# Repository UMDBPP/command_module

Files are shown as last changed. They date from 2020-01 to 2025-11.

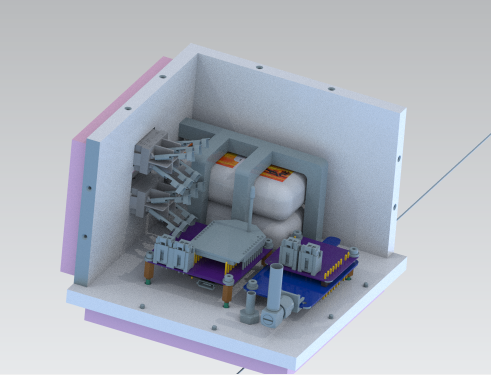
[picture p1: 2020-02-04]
Design_Review/images/cell_box.PNG

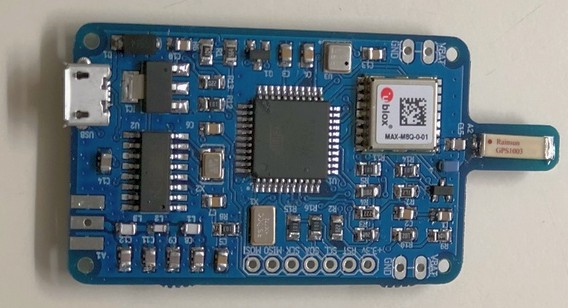
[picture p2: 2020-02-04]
Design_Review/images/lightaprs.jpg

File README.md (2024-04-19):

# ```</CMD>```

Command is the primary tracking payload flown by BPP. This repository contains design files and software required to run the current version of command.

Current POC:
Shipman

 ## Design Priciples
As the command module needs to fly on every flight mass reduction is a primary focus. For this reason a switch from perfboard to custom PCB's was done, and a substantial reduction in box volume is underway. Reliability is incredibly important and for this reason the payload operates its tracking systems in a full 4N redundant method.
### Tracking systems include (system/function):
#### 2x LiteAPRS 2m transmitters on 144.390 MHz
In flight position updates every minute. By nature of APRS tracking in hilly terrain unlikely to receive exact coordinates under 500m unless operating our own radios.
#### 1x SPOT Trace Tracker
COTS tracker from SPOT. Gives exact coordinates on landing.
#### 1x BITS (Balloon Iridium Telemetry System)
Exact coordinates throughout the flight, variable transmission rate 1min-15minutes (technically 10s-inf). Datalogger. XBee 900 HP allows for commands to be relayed through Iridium to other payloads and telemetry from payloads to be sent to ground. Possibility of ground to payload XBee communication without Iridium allowing for low latency high rate commanding.

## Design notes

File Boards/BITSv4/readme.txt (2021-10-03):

Folder for BITSv4 development
Starting 10/3/2021,
jmolter

Work based on lessons from BITSv3

---Focus Areas---

-Reg LMR16020-
Keep the IC
Change inductor for easier assembly
Consider chaning output to 5v,
OR source 5v from another source

-Misc.-
Change power connector to match LightAPRS LVC

Change picoblade to right angle

Remove celltracker crosstalk conn

Consider GPS improvements

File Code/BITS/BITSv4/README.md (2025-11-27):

# BITS (Balloon Iridium Telemetry System)
The UMDBPP Iridium payload, armed with an Iridium 9603 on a RockBlock carrier board for instantaneous Global Blackmagics

WIP: XBee Mesh net support for other payloads
     New PCB for smaller, lighter, better looking tracking
     Battery Voltage sensing for long haul flights

# Building Code
Hi, from the `BITS` folder, run `arduino-cli compile -e BITSv4` to do reproducible builds. I also created a Github Action that will automatically build the BITSv4 code when you push any changes to the master branch. You can find the build artifacts at [https://github.com/UMDBPP/command_module/releases](https://github.com/UMDBPP/command_module/releases).

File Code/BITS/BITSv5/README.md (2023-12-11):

# ```</BITSv5 Software>```

This folder contains the code needed to operate BITS (Balloon Iridium Telemetry System) Version 5. The below outlines the structure of the code. BITS Version 5 uses the RP2040 by the Raspberry Pi foundation and leverages the RP2040 Pico C SDK and build system meaning that this is not an Arduino based project!

The test project below currently features 3 executable binaries that are automatically built using a GitHub action. This is a proof of concept and enables the BITSv5 software to be built independent of any single user which makes the process of changing and rebuilding the project more approachable to everyone.

The action that builds the test project can be seen here: [https://github.com/UMDBPP/command_module/actions/workflows/build-BITSv5.yml](https://github.com/UMDBPP/command_module/actions/workflows/build-BITSv5.yml)

And the release product that it creates can be seen here: [https://github.com/UMDBPP/command_module/releases/tag/BITSv5-v0.0.0](https://github.com/UMDBPP/command_module/releases/tag/BITSv5-v0.0.0)

## Test
This is the current working space for developing BITSv5 software. Currently basic radio communications have been implemented and verified with hardware. Below are features that need to be implemented for a minimum viable product in the the next month or two.

[x] Basic long range radio communications

[] Serial console

[] Non-volatile configuration

[] GPS geolocation

[] Iridium interface and comms

## Radio Test
This is a future project designed to be a suite of tests that test the radio found on BITSv5. Not currently implemented.

## Pico-SDK
This is a submodule that pulls in the RP2040 SDK which is required to build all of the code found in this folder. It shouldn't need to be touched except for the occasional update.

More on the RP2040 C SDK can be found here: [https://www.raspberrypi.com/documentation/pico-sdk/](https://www.raspberrypi.com/documentation/pico-sdk/)

## Reference
This folder contains two useful documents from the Raspberry Pi Foundation about using the SDK above.

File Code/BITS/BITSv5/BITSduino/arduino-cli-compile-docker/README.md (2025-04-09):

# A Note

This is originally from https://github.com/MacroYau/arduino-cli-compile-docker. I made some modifications since I think the cli has changed since the repo was originally made. The reason that I recommend this build system is to avoid the messiness that comes with having different global libaries installed on different systems. Instead the build environment is created ad hoc as a docker container which means that it should be much easier for anyone to build the code.

-Shipman

# Arduino CLI Compile



Dockerized [`arduino-cli`](https://github.com/arduino/arduino-cli) sketch 
compilation tool with per-project core and library dependencies support.

## Getting Started

1.  Install [Docker Engine](https://docs.docker.com/install/) on your machine.

2.  Go to your Arduino sketch folder which contains the main `.ino` file.

3.  Create `project.yaml` with the following content:

    ```yaml
    # Filename of the project's main sketch
    sketch: Blink.ino
    # Sketch version (optional; appended to filename of compiled binary file)
    version: 1.0.0

    # Compilation target
    target:
      # Arduino core name
      core: arduino:samd            # Installs the latest version; or
      # core: arduino:samd==1.6.21  # Installs v1.6.21
      # Arduino board FQBN string (obtained from `arduino-cli board list`)
      board: arduino:samd:mkrzero
      # Additional board manager URL for core installation (optional)
      url: https://arduino.esp8266.com/stable/package_esp8266com_index.json

    # Libraries to be included for compilation
    libraries:
      - Arduino Low Power           # Installs the latest version; or
      # - Arduino Low Power==1.2.1  # Installs v1.2.1
    ```

4.  Download `arduino-cli-compile` to a `PATH` directory and make it executable.

5.  Run `arduino-cli-compile path/to/sketch/folder`.

6.  The compiled binary file will appear in `dist/` inside the sketch folder.

7.  Upload the compiled binary file to your Arduino board. This part is not 
    (yet) Dockerized. For example, you can use `arduino-cli` installed on your 
    machine connecting to the board:

    ```bash
    arduino-cli upload -p /dev/ttyACM0 -b arduino:samd:mkrzero -i path/to/bin/file
    ```

8.  Watch your board blinking!

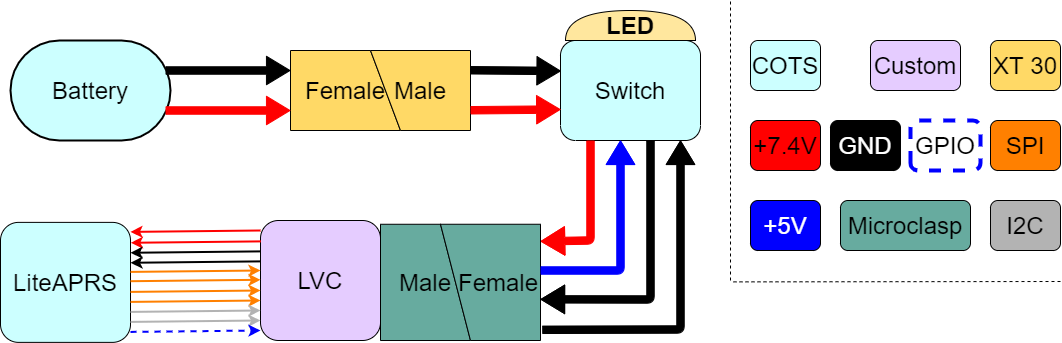
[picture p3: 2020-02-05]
Design_Review/images/liteaprs_block_diagram.png

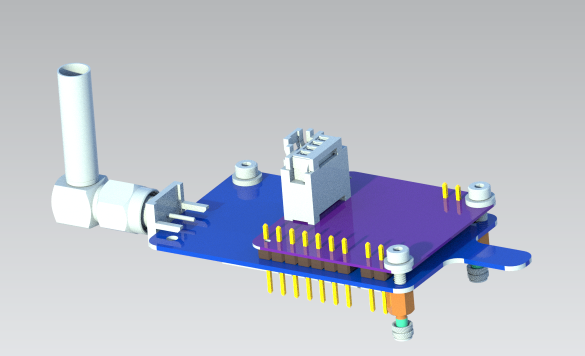
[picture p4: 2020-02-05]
Design_Review/images/LVC.PNG

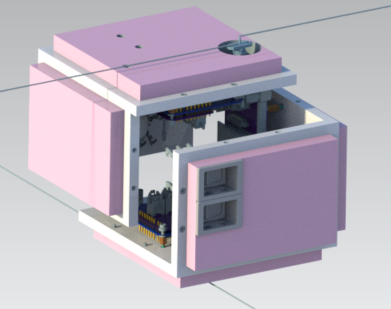
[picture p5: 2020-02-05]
Design_Review/images/opened_cmd.PNG

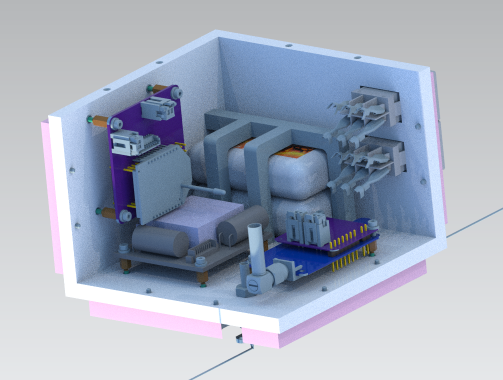
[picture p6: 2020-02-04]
Design_Review/images/iridium_box.PNG

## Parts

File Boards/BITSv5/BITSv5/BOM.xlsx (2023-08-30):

Part ID | Name | Function | Value | Package | Part Link | Cost
U1 | RP2040 | Microprocessor | - | - | https://www.digikey.com/en/products/detail/raspberry-pi/SC0914-13/14306010?s=N4IgTCBcDaIE4AcwAYAsyQF0C%2BQ | $0.70
U2 | W25Q128JVS | Flash Memory | 16MB | - | https://www.digikey.com/en/products/detail/winbond-electronics/W25Q128JVSIQ/5803943 | $1.68
U3 | MAX-M10S | GPS | - | MAX | https://www.digikey.com/en/products/detail/u-blox/MAX-M10S-00B/15712906 | $21.00
U4 | MAX25255AFDA/VY+ | Dual Buck | 3.3V, 5V | 23-WFQFN | https://www.digikey.com/en/products/detail/analog-devices-inc-maxim-integrated/max25255afda-vy/18693435 | $2.41
U6 | XBP9X-DMUS-001 | Xbee | 900 MHz | SMT | https://www.digikey.com/en/products/detail/digi/XBP9X-DMUS-001/5972744 | $112.59
U7 | TPS2121 | Power Mux Switch | 2:1 In:Out | 12-VFQFN | https://www.digikey.com/en/products/detail/texas-instruments/TPS2121RUXR/9859001 | $2.31
U8 | LTC6703 | LVC Comparator | 3V Cutoff | 3-DFN | https://www.digikey.com/en/products/detail/analog-devices-inc/LT6703HDC-3-TRMPBF/1590279 | $3.05
U9 | TVS1800 | Surge Protection | - | 6-WDFN | https://www.digikey.com/en/products/detail/texas-instruments/TVS1800DRVR/8601784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 | $0.65
U10 | USBLC6-2SC6 | Surge Protection | - | SOT-23-6 | https://www.digikey.com/en/products/detail/stmicroelectronics/USBLC6-2SC6/1040559 | $0.61
Y1 | ECS-120-10-36B2-JTN-TR | Crystal | 12 MHz | 2520 | https://www.digikey.com/en/products/detail/ecs-inc/ECS-120-10-36B2-JTN-TR/14663300 | $0.42
BT1 | XT30PW-M | Battery Connector | - | XT30
AE1 | 1575AT43A0040001E | GPS Antenna | 0.5-1 dB | Chip | https://www.digikey.com/en/products/detail/johanson-technology-inc/1575AT43A0040001E/1560674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 | $0.89
D1 |  | LED |  | 0603
J1 | Rockblock Connector | Iridium | 10-Pin | Molex PB | https://www.digikey.com/en/products/detail/molex/0532611071/699102 | $1.07 | must order connecting pieces
J2 | USB-C 2.0 Port | USB C Connection | - | GCT4085 | https://www.digikey.com/en/products/detail/gct/USB4085-GF-A/9859662 | $0.94
J3 | Headers | Debugging | - | Male Pins | - | -
SW2 | CAS-120TB | Memory Boot | - | - | https://www.digikey.com/en/products/detail/nidec-components-corporation/CAS-120TB/341662 | $1.37
SW3 | CL-SB-12B-01T | Power Slider | - | - | https://www.digikey.com/en/products/detail/nidec-components-corporation/CL-SB-12B-01T/3507823 | $1.26
Q1 |  | Transistor | PNP | SOT23-3
Q2 |  | Transistor | NPN | SOT23
R1 |  | R | 27 | 0402
R2 |  | R | 27 | 0603
R3 |  | R | 10K | 0603
R4 |  | R | 1K | 0603
R5 |  | R | 1K | 0402
R7 |  | R | 5.1K | 0603
R8 |  | R | 5.1K | 0603
R9 |  | R | 10K | 0603
R10 |  | R | 10K | 0603
R11 |  | R | 10K | 0603
R12 |  | R | 470 | 0603
R15 |  | R | 23.7K | 0603
R16 |  | R | 5K | 0603
R17 |  | R | 46.4K | 0603
R18 |  | R | 1.5M | 0603
R19 |  | R | 100K | 0603
R20 |  | R | 510K | 0603
R21 |  | R | 10K | 0603
R22 |  | R | 23.7K | 0603
R23 |  | R | 5K | 0603
R24 |  | R | 10K | 0603
C1 |  | C | 1 uF | 0402
C2 |  | C | 1 uF | 0402
C3 |  | C | 100 nF | 0402
C4 |  | C | 100 nF | 0402
C5 |  | C | 100 nF | 0402
C6 |  | C | 100 nF | 0402
C7 |  | C | 100 nF | 0402
C8 |  | C | 100 nF | 0402
C9 |  | C | 100 nF | 0402
C10 |  | C | 100 nF | 0402
C11 |  | C | 100 nF | 0402
C12 |  | C | 100 nF | 0603
C13 |  | C | 10 pF | 0603
C14 |  | C | 10 pF | 0603
C15 |  | C | 0.1 uF | 0603
C16 |  | C | 4.7 uF | 0603
C17 |  | C | 22 uF | 0603
C18 |  | C | 22 uF | 0603
C19 |  | C | 22 uF | 0603
C20 |  | C | 22 uF | 0603
C21 |  | C | 22 uF | 0603
C22 |  | C | 22 uF | 0603
C23 |  | C | 0.1 uF | 0603
C24 |  | C | 0.1 uF | 0603
C25 |  | C | 2.2 uF | 0603
C26 |  | C | 100 pF | 0603
C27 |  | C | 1 uF | 0603
C28 |  | C | 10 uF | 0603
C29 |  | C | 4.7 uF | 0603
C30 |  | C | 4.7 uF | 0603
C31 |  | C | 0.1 uF | 0603
C32 |  | C | 100 nF | 0603
C33 |  | C | 10 nF | 0603
C34 |  | C | 10 uF | 0603
C35 |  | C | 10 uF | 0603
C36 |  | C | 1 uF | 0603
C37 |  | C | 1 uF | 0603
L1 | 252012CDMCDDS-R47MC | L | 0.47 uH | 1008 | https://www.digikey.com/en/products/detail/sumida-america-inc/252012CDMCDDS-R47MC/9960783 | $0.55
L2 | 252012CDMCDDS-R47MC | L | 0.47 uH | 1008 | https://www.digikey.com/en/products/detail/sumida-america-inc/252012CDMCDDS-R47MC/9960783 | $0.55
 |  |  |  |  | Total | $152.05

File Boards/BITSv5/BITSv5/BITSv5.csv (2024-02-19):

Source: | /Users/michaelshipman/Developer/command_module/Boards/BITSv5/BITSv5/BITSv5.kicad_sch
Date: | 2024 February 18, Sunday 18:52:49
Tool: | Eeschema 7.0.5-0
Generator: | /Applications/KiCad/KiCad.app/Contents/SharedSupport/plugins/bom_csv_grouped_by_value_with_fp.py
Component Count: | 103
Ref | Qnty | Value | Cmp name | Footprint | Description | Vendor | DNP
B1 | 1 | KMR2 | SW_Push | Button_Switch_SMD:SW_Push_1P1T_NO_CK_KMR2 | Push button switch, generic, two pins
BT2 | 1 | 3V | Battery_Cell | BITSv5:SEIKO_ML414H_IV01E | Single-cell battery
C1, C2 | 2 | 1uF | C_Small | Capacitor_SMD:C_0402_1005Metric | Unpolarized capacitor, small symbol
C3, C4, C5, C6, C7, C8, C9, C10, C11, C12, C32 | 11 | 100nF | C_Small | Capacitor_SMD:C_0402_1005Metric | Unpolarized capacitor, small symbol
C13, C14 | 2 | 10pF | C_Small | Capacitor_SMD:C_0402_1005Metric | Unpolarized capacitor, small symbol
C15, C26, C34 | 3 | 10uF | C_Small | Capacitor_SMD:C_0603_1608Metric | Unpolarized capacitor, small symbol
C16, C17, C24, C27, C33, C39, C40 | 7 | 1uF | C_Small | Capacitor_SMD:C_0603_1608Metric | Unpolarized capacitor, small symbol
C18, C20 | 2 | 47uF | C_Small | Capacitor_SMD:C_1206_3216Metric | Unpolarized capacitor, small symbol
C19, C23, C29, C30 | 4 | 100nF | C_Small | Capacitor_SMD:C_0603_1608Metric | Unpolarized capacitor, small symbol
C21 | 1 | 4.7uF | C_Small | Capacitor_SMD:C_0805_2012Metric | Unpolarized capacitor, small symbol
C25, C31 | 2 | 22uF | C_Small | Capacitor_SMD:C_0805_2012Metric | Unpolarized capacitor, small symbol
C28, C38 | 2 | 15uF | C_Small | Capacitor_SMD:C_1206_3216Metric | Unpolarized capacitor, small symbol
D1 | 1 | LED | LED | LED_SMD:LED_0603_1608Metric | Light emitting diode
D2 | 1 | 0.5A/40V/240mV | D_Schottky_Small | Diode_SMD:D_SOD-123F | Schottky diode, small symbol
H1, H2, H3 | 3 | M2 | MountingHole_Pad | MountingHole:MountingHole_2.2mm_M2_Pad | Mounting Hole with connection
J1 | 1 | Conn_01x03_Pin | Conn_01x03_Pin | Connector_PinHeader_2.54mm:PinHeader_1x03_P2.54mm_Vertical | Generic connector, single row, 01x03, script generated
J2 | 1 | USB_C_Receptacle_USB2.0 | USB_C_Receptacle_USB2.0 | Connector_USB:USB_C_Receptacle_GCT_USB4105-xx-A_16P_TopMnt_Horizontal | USB 2.0-only Type-C Receptacle connector
J3 | 1 | XT30 | Conn_01x02 | Connector_AMASS:AMASS_XT30PW-M_1x02_P2.50mm_Horizontal | Generic connector, single row, 01x02, script generated (kicad-library-utils/schlib/autogen/connector/)
J4 | 1 | PicoBlade_53261-1071 | Conn_01x10_Pin | Connector_Molex:Molex_PicoBlade_53261-1071_1x10-1MP_P1.25mm_Horizontal | Generic connector, single row, 01x10, script generated
J5, J6 | 2 | U.FL | Conn_Coaxial | Connector_Coaxial:U.FL_Molex_MCRF_73412-0110_Vertical | coaxial connector (BNC, SMA, SMB, SMC, Cinch/RCA, LEMO, ...)
JP1 | 1 | SolderJumper_2_Open | SolderJumper_2_Open | Jumper:SolderJumper-2_P1.3mm_Open_RoundedPad1.0x1.5mm | Solder Jumper, 2-pole, open
L3, L4 | 2 | 3.3uH | L_Small | Inductor_SMD:L_1210_3225Metric | Inductor, small symbol
Q1 | 1 | Q_NMOS_GSD | Q_NMOS_GSD | Package_TO_SOT_SMD:SOT-23-3 | N-MOSFET transistor, gate/source/drain
R1, R2 | 2 | 27 | R_Small | Resistor_SMD:R_0402_1005Metric | Resistor, small symbol
R3, R6, R9, R22, R27 | 5 | DNF | R_Small | Resistor_SMD:R_0603_1608Metric | Resistor, small symbol
R4 | 1 | 1K | R_Small | Resistor_SMD:R_0603_1608Metric | Resistor, small symbol
R5 | 1 | 1K | R_Small | Resistor_SMD:R_0402_1005Metric | Resistor, small symbol
R7, R8 | 2 | 5.1K | R_Small | Resistor_SMD:R_0603_1608Metric_Pad0.98x0.95mm_HandSolder | Resistor, small symbol
R10, R13 | 2 | 100m | R_Small | Resistor_SMD:R_0603_1608Metric | Resistor, small symbol
R11 | 1 | 10k | R_Small | Resistor_SMD:R_0603_1608Metric | Resistor, small symbol
R12 | 1 | 470 | R_Small | Resistor_SMD:R_0603_1608Metric | Resistor, small symbol
R14 | 1 | 3.3K | R_Small | Resistor_SMD:R_0603_1608Metric | Resistor, small symbol
R15 | 1 | 332k | R_Small | Resistor_SMD:R_0603_1608Metric | Resistor, small symbol
R16, R20, R31 | 3 | 100k | R_Small | Resistor_SMD:R_0603_1608Metric | Resistor, small symbol
R17 | 1 | 44.2K | R_Small | Resistor_SMD:R_0603_1608Metric | Resistor, small symbol
R21, R24 | 2 | 10K | R_Small | Resistor_SMD:R_0603_1608Metric | Resistor, small symbol
R23, R28 | 2 | 0 | R_Small | Resistor_SMD:R_0603_1608Metric | Resistor, small symbol
R25 | 1 | 10.2k | R_Small | Resistor_SMD:R_0603_1608Metric | Resistor, small symbol
R26 | 1 | 5k | R_Small | Resistor_SMD:R_0603_1608Metric | Resistor, small symbol
R29 | 1 | 15k | R_Small | Resistor_SMD:R_0603_1608Metric | Resistor, small symbol
R30 | 1 | 47.5k | R_Small | Resistor_SMD:R_0603_1608Metric | Resistor, small symbol
R32 | 1 | 25.5k | R_Small | Resistor_SMD:R_0603_1608Metric | Resistor, small symbol
R33 | 1 | 43.2k | R_Small | Resistor_SMD:R_0603_1608Metric | Resistor, small symbol
SW2 | 1 | ~ | SW_SPDT | BITSv5:CAS-120TB_NDC-M | Switch, single pole double throw
SW3 | 1 | SLIDE | SW_SPDT | BITSv5:CL-SB-12B-01_NDC | Switch, single pole double throw
TP1, TP2 | 2 | TestPoint | TestPoint | TestPoint:TestPoint_Pad_D2.0mm | test point
TP4, TP5, TP6 | 3 | TestPoint | TestPoint | TestPoint:TestPoint_Keystone_5000-5004_Miniature | test point
U1 | 1 | MCU_RaspberryPi_RP2040_RP2040 | MCU_RaspberryPi_RP2040 | BITSv5:RP2040-QFN-56
U2 | 1 | W25Q128JVS | W25Q128JVS | BITSv5:WSON_128JVPIQ_WIN | 128Mb Serial Flash Memory, Standard/Dual/Quad SPI, SOIC-8
U3 | 1 | MAX-M10S | MAX-M10S | RF_GPS:ublox_MAX | GNSS Module MAX M10, VCC 1.65V to 3.6V
U4 | 1 | DRF1262TL | DRF1262TL | BITSv5:DRF1262TL
U5, U8 | 2 | TPSM33625FRDNR | TPSM33625 | BPP_Lib:RDN0011A-MFG-NO-VIA
U6 | 1 | TPS2121RUXR | TPS2121RUXR | BITSv5:TPS2121
U7 | 1 | MB85RS1MT | MB85RS1MT | BPP_Lib:BGA8CP30X40_5X3_309X228X35B25N | FRAM memory with SPI interface, SOIC-8 SON-8
U9 | 1 | TVS1800DRVR | TVS1800DRVR | BITSv5:TVS1800
U10 | 1 | USBLC6-2SC6 | USBLC6-2SC6 | BITSv5:SOT23-6L_STM
U11 | 1 | MS5607-02BA | MS5607-02BA | Package_LGA:LGA-8_3x5mm_P1.25mm | Barometric pressure sensor, 20cm resolution, 10 to 1200 mbar, I2C and SPI interface up to 20MHz, LGA-8
Y1 | 1 | 12MHz | Crystal_GND24_Small | Crystal:Crystal_SMD_2520-4Pin_2.5x2.0mm | Four pin crystal, GND on pins 2 and 4, small symbol

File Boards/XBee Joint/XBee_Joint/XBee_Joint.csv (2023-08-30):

Source: | C:\Storage\BPP\Command\command_module\Boards\XBee Joint\XBee_Joint\XBee_Joint.kicad_sch
Date: | 8/29/2023 1:57:28 PM
Tool: | Eeschema 7.0.2
Generator: | C:\Program Files\KiCad\7.0\bin\scripting\plugins/bom_csv_grouped_by_value.py
Component Count: | 63
Collated Components:
Item | Qty | Reference(s) | Value | LibPart | Footprint | Datasheet | DNP | AVAILABILITY | Check_prices | DESCRIPTION | DIGIKEY-PURCHASE-URL | Description | DigiKey_Part_Number | MANUFACTURER | MAXIMUM_PACKAGE_HEIGHT | MF | MFANUFACTURER | MOUSER-PURCHASE-URL | MP | PACKAGE | PARTREV | PRICE | Package | Purchase-URL | STANDARD | SnapEDA_Link | TEXAS_INSTRUMENTS-PURCHASE-URL
1 | 1 | BT1 | 1S1P LiPo | Device:Battery_Cell | BITSv5:1042_KEY | ~
2 | 10 | C1, C2, C5, C6, C7, C8, C9, C11, C12, C13 | 100nF | Device:C | Capacitor_SMD:C_0402_1005Metric_Pad0.74x0.62mm_HandSolder | ~
3 | 2 | C3, C4 | 1uF | Device:C | Capacitor_SMD:C_0402_1005Metric_Pad0.74x0.62mm_HandSolder | ~
4 | 5 | C10, C20, C23, C24, C25 | 10uF | Device:C | Capacitor_SMD:C_0603_1608Metric_Pad1.08x0.95mm_HandSolder | ~
5 | 2 | C14, C19 | 1uF | Device:C | Capacitor_SMD:C_0603_1608Metric_Pad1.08x0.95mm_HandSolder | ~
6 | 1 | C15 | 100pF | Device:C | Capacitor_SMD:C_0603_1608Metric_Pad1.08x0.95mm_HandSolder | ~
7 | 2 | C16, C26 | 100nF | Device:C | Capacitor_SMD:C_0603_1608Metric_Pad1.08x0.95mm_HandSolder | ~
8 | 2 | C17, C18 | 10pF | Device:C | Capacitor_SMD:C_0603_1608Metric_Pad1.08x0.95mm_HandSolder | ~
9 | 2 | C21, C22 | 1uF | Device:C_Small | Capacitor_SMD:C_0603_1608Metric_Pad1.08x0.95mm_HandSolder | ~
10 | 3 | C27, C28, C29 | 22uF | Device:C | Capacitor_SMD:C_0603_1608Metric_Pad1.08x0.95mm_HandSolder | ~
11 | 1 | D1 | LED | Device:LED | LED_SMD:LED_0603_1608Metric | ~
12 | 1 | J1 | Conn_01x07 | Connector_Generic:Conn_01x07 | Connector_PinSocket_2.54mm:PinSocket_1x07_P2.54mm_Vertical | ~
13 | 1 | J2 | USB_C_Receptacle_USB2.0 | Connector:USB_C_Receptacle_USB2.0 | Connector_USB:USB_C_Receptacle_GCT_USB4085 | https://www.usb.org/sites/default/files/documents/usb_type-c.zip
14 | 1 | L1 | 1.5uH | Device:L | Inductor_SMD:L_Coilcraft_XxL4040 | ~
15 | 1 | Q1 | Q_NMOS_GSD | Device:Q_NMOS_GSD | Package_TO_SOT_SMD:SOT-23-3 | ~
16 | 2 | R1, R5 | 10K | Device:R | Resistor_SMD:R_0603_1608Metric_Pad0.98x0.95mm_HandSolder | ~
17 | 2 | R2, R3 | 27Ω | Device:R | Resistor_SMD:R_0402_1005Metric_Pad0.72x0.64mm_HandSolder | ~
18 | 1 | R4 | 1K | Device:R | Resistor_SMD:R_0603_1608Metric_Pad0.98x0.95mm_HandSolder | ~
19 | 1 | R6 | 1K | Device:R | Resistor_SMD:R_0402_1005Metric_Pad0.72x0.64mm_HandSolder | ~
20 | 2 | R7, R8 | 5.1K | Device:R | Resistor_SMD:R_0603_1608Metric_Pad0.98x0.95mm_HandSolder | ~
21 | 1 | R9 | 470 | Device:R | Resistor_SMD:R_0603_1608Metric_Pad0.98x0.95mm_HandSolder | ~
22 | 1 | R11 | 1.05M | Device:R | Resistor_SMD:R_0603_1608Metric_Pad0.98x0.95mm_HandSolder | ~
23 | 1 | R12 | 154K | Device:R | Resistor_SMD:R_0603_1608Metric_Pad0.98x0.95mm_HandSolder | ~
24 | 1 | R13 | 46.4K | Device:R | Resistor_SMD:R_0603_1608Metric_Pad0.98x0.95mm_HandSolder | ~
25 | 3 | R14, R15, R16 | 10K | Device:R_Small | Resistor_SMD:R_0603_1608Metric_Pad0.98x0.95mm_HandSolder | ~
26 | 1 | R17 | 22K | Device:R_Small | Resistor_SMD:R_0603_1608Metric_Pad0.98x0.95mm_HandSolder | ~
27 | 1 | R18 | 510K | Device:R | Resistor_SMD:R_0603_1608Metric_Pad0.98x0.95mm_HandSolder | ~
28 | 1 | SW1 | ~ | Switch:SW_SPDT | BITSv5:CAS-120TB_NDC-M | ~
29 | 1 | SW2 | SLIDE | Switch:SW_SPDT | BITSv5:CL-SB-12B-01_NDC | ~
30 | 1 | U1 | MCU_RaspberryPi_RP2040_RP2040 | RP2040_minimal-cache:MCU_RaspberryPi_RP2040_RP2040 | BITSv5:RP2040-QFN-56
31 | 1 | U2 | XBee_SMT | BITSv5:XBP9X-DMUS-001 | BITSv5:XCVR_XBP9X-DMUS-001 | http://www.digi.com/resources/documentation/digidocs/pdfs/90002126.pdf |  |  | https://www.snapeda.com/parts/XBP9X-DMUS-001/Digi+International/view-part/?ref=eda |  |  | General ISM < 1GHz - Transceiver Module 902MHz ~ 928MHz Antenna Not Included, U.FL Surface Mount | 602-1890-ND | Digi | 3.556mm | Digi International |  |  | XBP9X-DMUS-001 |  | K |  | Module Digi International | https://pricing.snapeda.com/search?q=XBP9X-DMUS-001&ref=eda | Manufacturer recommendations | https://www.snapeda.com/parts/XBP9X-DMUS-001/Digi+International/view-part/?ref=snap
32 | 1 | U3 | W25Q128JVS | Memory_Flash:W25Q128JVS | Package_SO:SOIC-8_5.23x5.23mm_P1.27mm | http://www.winbond.com/resource-files/w25q128jv_dtr%20revc%2003272018%20plus.pdf
33 | 1 | U4 | USBLC6-2SC6 | USBLC6-2SC6:USBLC6-2SC6 | BITSv5:SOT23-6L_STM-M | USBLC6-2SC6
34 | 1 | U5 | TPS63021DSJR | BITSv5:TPS63021DSJR | IC_TPS63021DSJR |  |  | Good | https://www.snapeda.com/parts/TPS63021DSJR/Texas+Instruments/view-part/?ref=eda | High Efficiency Single Inductor Buck-Boost Converter with 4A Switch 14-VSON -40 to 85 | https://snapeda.com/shop?store=DigiKey&id=296571 | High Efficiency Single Inductor Buck-Boost Converter with 4A Switch | 296-27259-2-ND |  | 1.00mm | Texas Instruments | Texas Instruments | https://snapeda.com/shop?store=Mouser&id=296571 | TPS63021DSJR | VSON-14 Texas Instruments | I | None | VSON-14 Texas Instruments | https://pricing.snapeda.com/search?q=TPS63021DSJR&ref=eda | Manufacturer Recommendations | https://www.snapeda.com/parts/TPS63021DSJR/Texas+Instruments/view-part/?ref=snap | https://snapeda.com/shop?store=Texas+Instruments&id=296571
35 | 1 | U6 | LT6703CDC-3 | LTC6703:LT6703CDC-3-TRPBF | BITSv5:DFN-3_DC_LIT | LT6703CDC-3-TRPBF
36 | 1 | U7 | TVS1800DRVR | TVS1800:TVS1800DRVR | BITSv5:TVS1800 | TVS1800DRVR
37 | 1 | U8 | TPS2121RUXR | TPS2121:TPS2121RUXR | BITSv5:TPS2121 | TPS2121RUXR
38 | 1 | Y1 | 12MHz | Device:Crystal_GND24 | Crystal:Crystal_SMD_2520-4Pin_2.5x2.0mm | ~

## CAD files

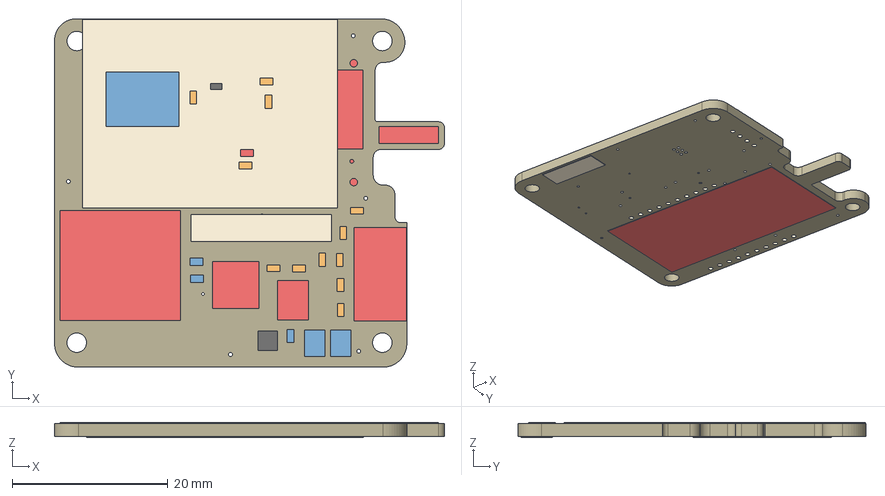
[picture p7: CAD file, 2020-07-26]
Boards/BITS3.2/bits3.2.step
50.0 x 44.7 x 1.87 mm
Board
TEENSY_3.1-3.2_OUTER_ROW
Red
MAX-M8
1.575GHz
0.2F
RB520S30T1GOSCT-ND
MICRO_SD
ASPI-6045S-560M-TCT-ND
10 uF x 3
2.2 uF x 2
LMR16020
DO-214AC
XBEE-PRO
MICROCLASP_4

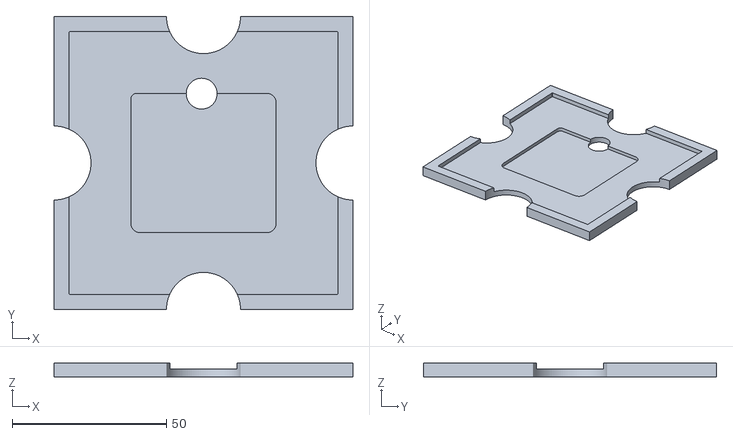
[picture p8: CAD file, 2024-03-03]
Boards/BITSv5/BITSv5.1-stencil-frame-02-02-2024/out.stl
97.0 x 95.0 x 4.60

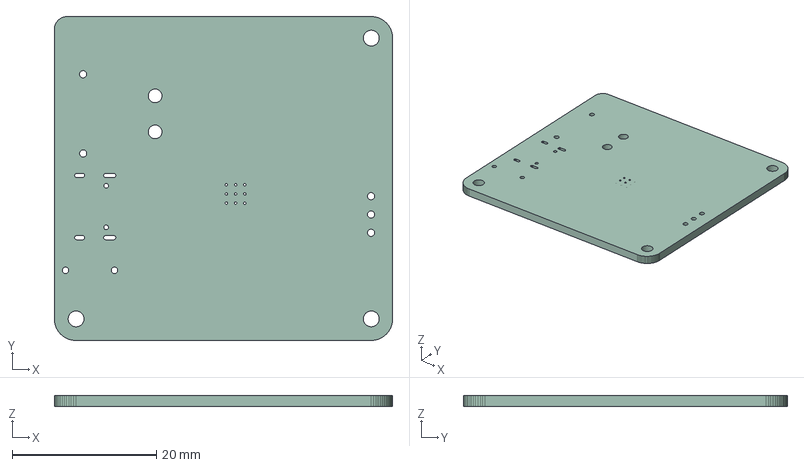
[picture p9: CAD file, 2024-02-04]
Boards/BITSv5/BITSv5/Models-Drawings/BITSv5-1.step
47.0 x 45.0 x 1.58 mm

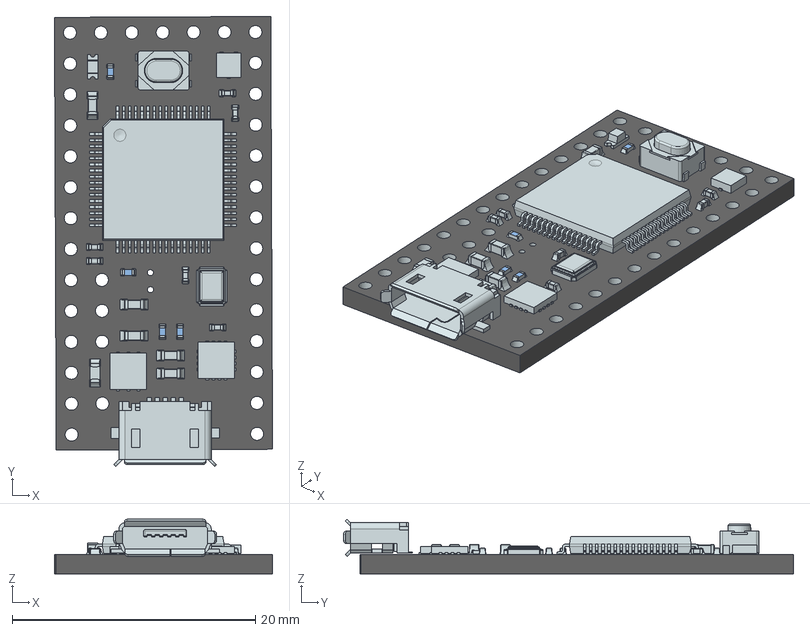
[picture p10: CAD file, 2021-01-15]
Boards/bored_cad/Teensy3_1.stp
17.9 x 37.0 x 4.49 mm
board
Group#12 (1) x 5
micro_usb_plastic (1)
micro_usb_shell (1)
lead
package (1)
lead (3) x 64
package
lead (1)
cap0402 v2 x 6
lead (2)
diode_0402 v1 x 4
cap0603_03 v3 x 5
smt_led_0805 v2
resistor_0603 v3

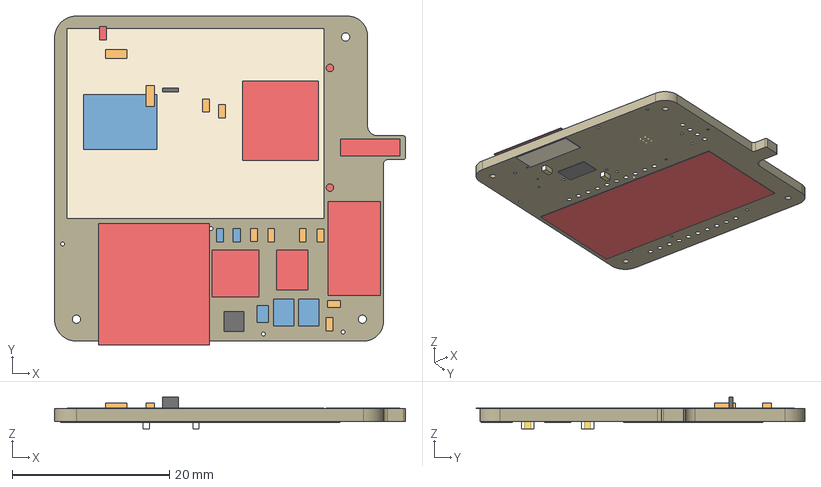
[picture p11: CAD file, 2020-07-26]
Boards/CellTracker_v3.2/cell_3.2.step
44.7 x 41.9 x 4.02 mm
Board
TEENSY_3.1-3.2_OUTER_ROW
MAX-M8
1.575GHz
XBEE-LTE-M
Green
2.2 uF x 2
0.1 uF
10 uF x 2
LMR16020
DO-214AC
ASPI-6045S-560M-TCT-ND
MICRO_SD
MICROCLASP_4
0.3F
RB520S30T1G
ISO7021
0.1uF x 2

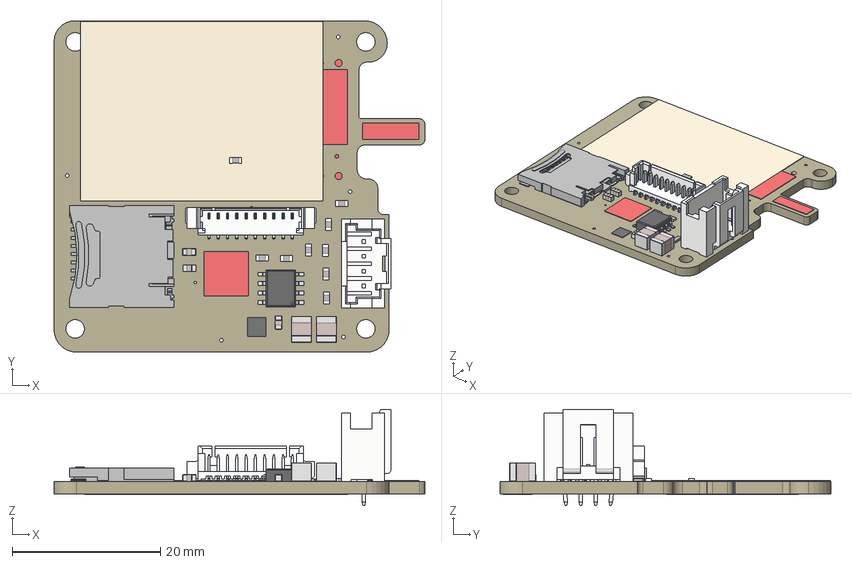
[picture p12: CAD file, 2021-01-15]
CAD/Electronics/bits3.2 v6.step
50.0 x 44.7 x 12.9 mm
Board
TEENSY_3.1-3.2_OUTER_ROW
Red
MAX-M8
1.575GHz
0.2F
RB520S30T1GOSCT-ND
MICRO_SD
ASPI-6045S-560M-TCT-ND
10 uF x 3
2.2 uF x 2
LMR16020
DO-214AC
XBEE-PRO
MICROCLASP_4

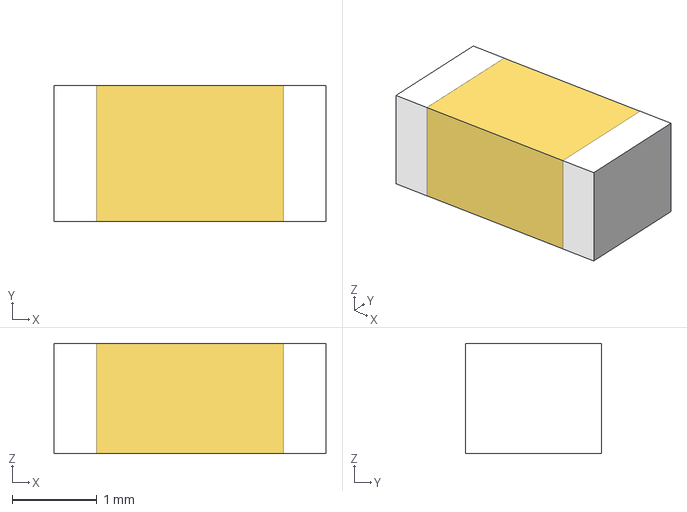
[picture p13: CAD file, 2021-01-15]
Boards/bored_cad/C1206.step
3.20 x 1.60 x 1.30 mm

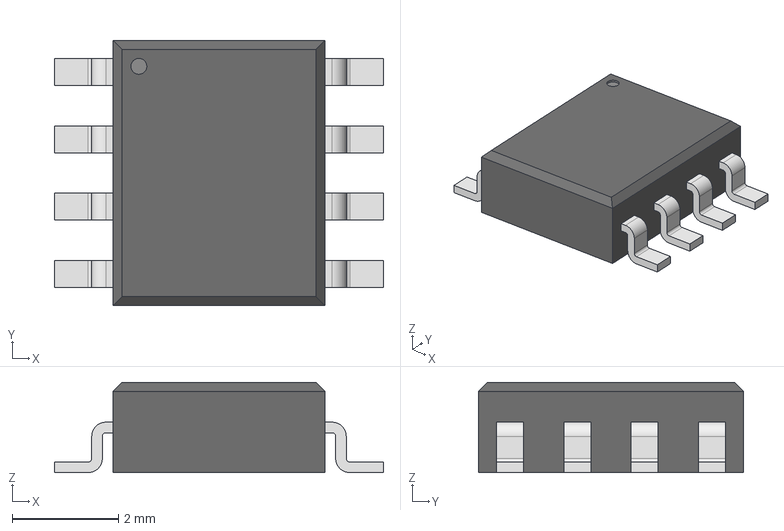
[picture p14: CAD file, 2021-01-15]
Boards/bored_cad/SOIC127P600X170-9T256X345N.step
6.20 x 5.00 x 1.70 mm

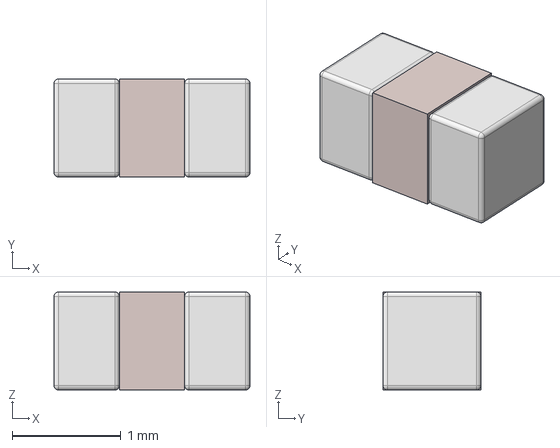
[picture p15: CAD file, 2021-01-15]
Boards/bored_cad/C0603.step
1.80 x 0.9 x 0.9 mm

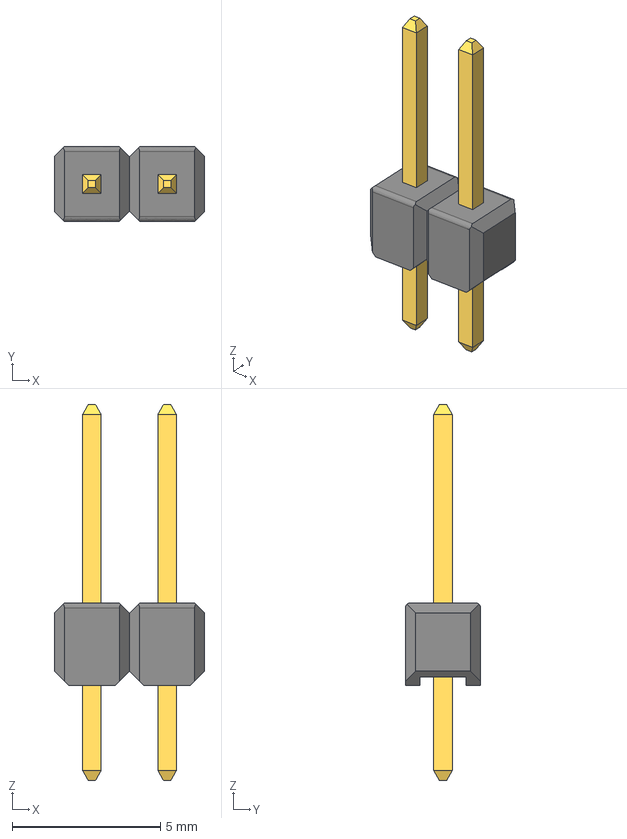
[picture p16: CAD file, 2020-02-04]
CAD/Electronics/Pin Header 1x2 TH Pitch 2.54mm.stp
5.08 x 2.54 x 12.7 mm

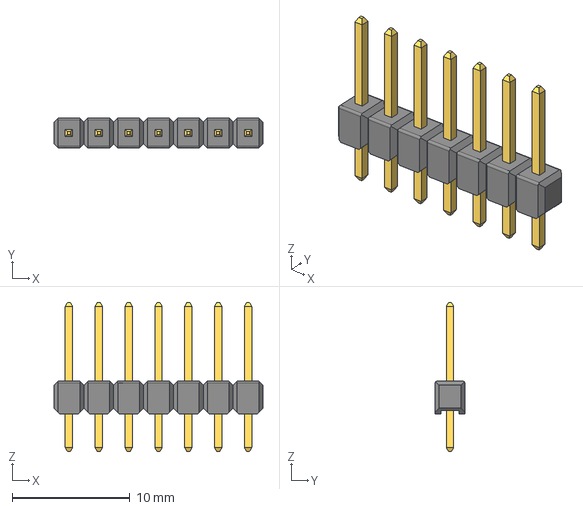
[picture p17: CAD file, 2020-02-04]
CAD/Electronics/Pin Header 1x7 TH Pitch 2.54mm.stp
17.8 x 2.54 x 12.7 mm

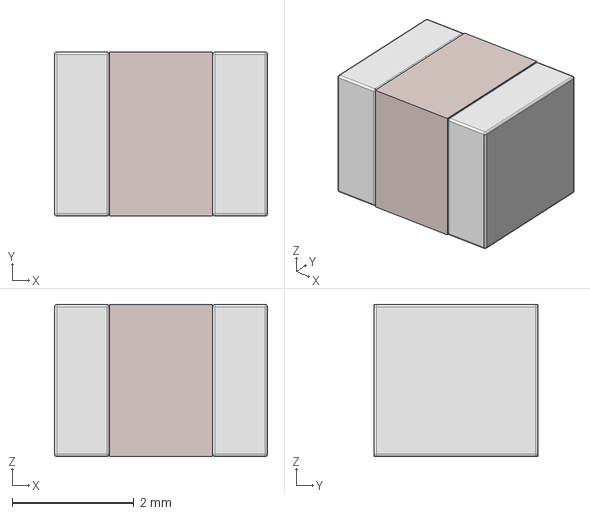
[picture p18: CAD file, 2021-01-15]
Boards/bored_cad/C1210.step
3.50 x 2.70 x 2.50 mm

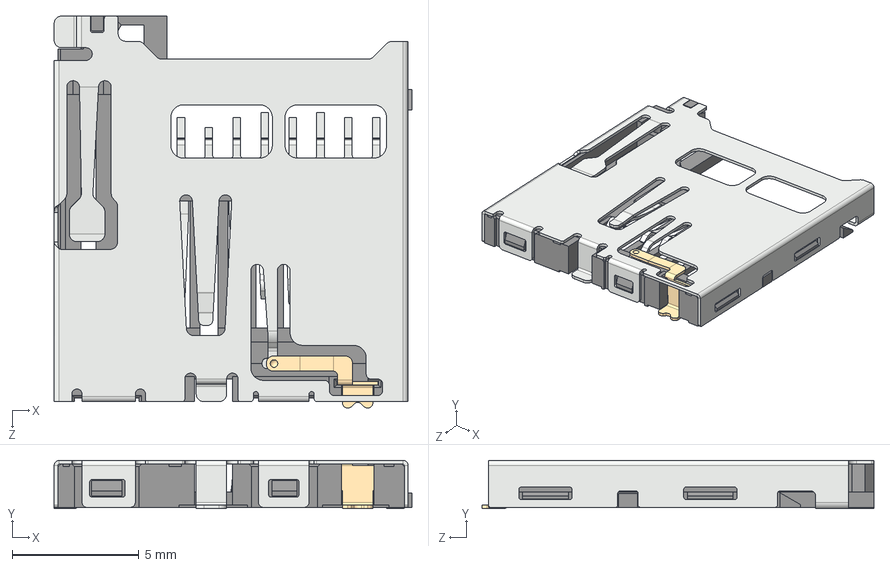
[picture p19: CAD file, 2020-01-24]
CAD/Electronics/micro SD Card Slot.step
14.1 x 1.90 x 15.5 mm
microSD_Body
microSD_Cover
microSD_Card_Detect
microSD_Pin_11.15 x 5
microSD_Pin_11.35 x 2
microSD_Pin_10.75

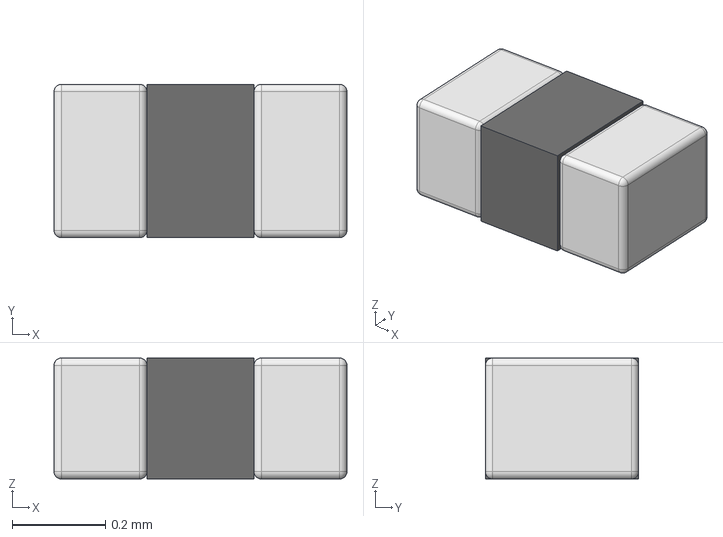
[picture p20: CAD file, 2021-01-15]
Boards/bored_cad/RESC0603X26.step
0.63 x 0.33 x 0.26 mm

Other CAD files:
Boards/BITS3.2/bits3.2_2020-07-09/CAMOutputs/bits3.2.step
Boards/bored_cad/DM3CS_MicroSD.step
Boards/BITS3.2/bits3.2_2020-07-09/CAMOutputs/0.2F.prt
Boards/BITS3.2/bits3.2_2020-07-09/CAMOutputs/1.575GHz.prt
Boards/BITS3.2/bits3.2_2020-07-09/CAMOutputs/10 uF.prt
Boards/BITS3.2/bits3.2_2020-07-09/CAMOutputs/2.2 uF.prt
Boards/BITS3.2/bits3.2_2020-07-09/CAMOutputs/22.prt
Boards/BITS3.2/bits3.2_2020-07-09/CAMOutputs/470.prt
Boards/BITS3.2/bits3.2_2020-07-09/CAMOutputs/53261-04.prt
Boards/BITS3.2/bits3.2_2020-07-09/CAMOutputs/53398-10.prt
Boards/BITS3.2/bits3.2_2020-07-09/CAMOutputs/ASPI-6045S-560M-TCT-ND.prt
Boards/BITS3.2/bits3.2_2020-07-09/CAMOutputs/Board.prt
Boards/BITS3.2/bits3.2_2020-07-09/CAMOutputs/DO-214AC.prt
Boards/BITS3.2/bits3.2_2020-07-09/CAMOutputs/LMR16020.prt
Boards/BITS3.2/bits3.2_2020-07-09/CAMOutputs/MAX-M8.prt
Boards/BITS3.2/bits3.2_2020-07-09/CAMOutputs/MICROCLASP_4.prt
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

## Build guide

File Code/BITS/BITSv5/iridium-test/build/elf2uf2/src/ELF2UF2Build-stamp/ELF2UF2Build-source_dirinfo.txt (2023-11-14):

# This is a generated file and its contents are an internal implementation detail.
# The download step will be re-executed if anything in this file changes.
# No other meaning or use of this file is supported.

method=source_dir
command=
source_dir=/Users/michaelshipman/Developer/command_module/Code/BITS/BITSv5/pico-sdk/tools/elf2uf2
work_dir=

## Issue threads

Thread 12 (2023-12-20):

RP2040 GPS driver

michaelshipman, 2023-12-20:

michaelshipman, 2023-12-20:
Going to start with some test hardware, RP2040 feather and a random NEO M8N board I found in the lab

michaelshipman, 2023-12-20:
Will be using these for note-taking - **starting with M8 test hardware**

Using I2C compliant DDC interface, default address is `0x42`

https://www.u-blox.com/en/product/neo-m8-series?legacy=Current#Documentation-&-resources
https://content.u-blox.com/sites/default/files/NEO-8Q-NEO-M8-FW3_HIM_UBX-15029985.pdf
https://content.u-blox.com/sites/default/files/products/documents/u-blox8-M8_ReceiverDescrProtSpec_UBX-13003221.pdf

michaelshipman, 2023-12-20:
### Reading
3 registers can be read from over the DDC interface, registers 253-255

`0xFD` and `0xFE` are the number of bytes that can be read and `0xFF` allows the data stream to be read, if no data available then `0xff` returned

Will likely want random access reading which lets you specify the register to read each time

`RW` bit - low for write access, high for read access

**Random Read Access**
- Start condition
- 7 bit address
- RW bit low
- 8 bit register address
- Receiver ACK
- Start condition
- 7 bit address
- RW bit high
- read 1 to N bytes
- NACK and stop condition to stop

michaelshipman, 2023-12-20:
### Writing

Writing just for UBX and NMEA messages for config data and other stuff, the registers aren't writable

> Following the start condition from the master, the 7-bit device address and the RW bit (which is a logic low for write access) are clocked onto the bus by the master transmitter. The receiver answers with an acknowledge (logic low) to indicate that it is responsible for the given address. Now, the master can write 2 to N bytes to the receiver, generating a stop condition after the last byte being written. The number of data bytes must be at least 2 to properly distinguish from the write access to set the address counter in random read accesses.

- 7-bit address
- RW bit low
- 2 to N bytes
- Stop condition

michaelshipman, 2023-12-20:
### Dynamic Platform Models

Will need to use one of the airborne models since those are the only ones with permissive max altitude, probably `Airborne <2g` to start with

michaelshipman, 2023-12-20:
Let's try a test with the `UBX-INF-DEBUG` message, should return some debug info

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

michaelshipman, 2023-12-20:
### UBX Checksum

Calculated over the message from the class to the end of the payload

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
```
CK_A = 0, CK_B = 0
for (i = 0; I < n; i++) {
    CK_A = CK_A + buffer[I];
    CK_B = CK_B + CK_A;
}
```

michaelshipman, 2023-12-20:
Ok well I can definitely read something over I2C, it doesn't quite make sense what I'm getting back yet

michaelshipman, 2023-12-21:
Ok so it looks like this device is sitting at address `0x0F` which is a bit weird but not really an issue.

I'm sending some different poll request messages but I keep getting something like `16 29 15 2 6 10 ff` if I read without specifying a register and something even weirder if I do specify a register (for instance the registers that indicate the number of bytes available to be read come back as `ff`)

I also tried the SparkFun Arduino library which couldn't seem to connect to it

Since this is just random garbage I pulled out of the lab it's entirely possible that it's cooked

May try another Arduino library later to see what happens but am going to focus on other things until I have actual BITS hardware

michaelshipman, 2023-12-23:
Ok so it definitely isn't cooked, it's spitting out plenty of NMEA strings over the UART connection.

Just need to figure out how to configure it properly, sometimes it will stop sending NMEA data if I ask it to and sometimes not, and when it does work it doesn't persist through a power cycle which would be nice.

In other news u-center is very useful for creating NMEA and UBX messages that are known good.

michaelshipman, 2023-12-23:
Ok so I need to actually read the documentation it seems

First of all, with a 10 second start up delay it seems that disabling NMEA on UART consistently works with the following NMEA message `$PUBX,41,1,0001,0001,9600,0*14\r\n` which is lovely.

Then I generated the UBX message `0xB5, 0x62, 0x06, 0x00, 0x14, 0x00, 0x01, 0x00, 0x00, 0x00, 0xD0, 0x08, 0x00, 0x00, 0x80, 0x25, 0x00, 0x00, 0x01, 0x00, 0x01, 0x00, 0x00, 0x00, 0x00, 0x00, 0x9A, 0x79` which provided me with a nice ACK UBX message

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

Lastly, it is worth noting that the **payload length field is a 2-byte little endian value,** which I had failed to internalize the first time around. thank god for u-center is all I can say, also little endian seems weird

michaelshipman, 2023-12-23:
Looks like the below has permanently disabled NMEA on UART by saving to the flash, both UBX messages got an ACK

```
const uint8_t
        message4[28] = {0xB5, 0x62, 0x06, 0x00, 0x14, 0x00, 0x01, 0x00,
                        0x00, 0x00, 0xD0, 0x08, 0x00, 0x00, 0x80, 0x25,
                        0x00, 0x00, 0x01, 0x00, 0x01, 0x00, 0x00, 0x00,
                        0x00, 0x00, 0x9A, 0x79};  // UBX message to do the same
                                                  // as the NMEA message below,
                                                  // was here just to see if I
                                                  // could get an ACK, which I
                                                  // did

    const uint8_t save_msg[21] = {0xB5, 0x62, 0x06, 0x09, 0x0D, 0x00,
                                  0x00, 0x00, 0x00, 0x00, 0xFF, 0xFF,
                                  0x00, 0x00, 0x00, 0x00, 0x00, 0x00,
                                  0x03, 0x1D, 0xAB};  // UBX message to save
                                                      // current config to
                                                      // battery backed RAM and
                                                      // flash

    const char *message2 =
        "$PUBX,41,1,0001,0001,9600,0*14\r\n";  // NMEA message that enables only
                                               // UBX on UART

    printf("Sending config\n");

    uart_write_blocking(uart0, (uint8_t *)message2, 32);
    uart_write_blocking(uart0, message4, 28);
    sleep_ms(100); // next message won't get an ACK unless a delay is here, 100 worked but could probably be shorted
    uart_write_blocking(uart0, save_msg, 21);
```

michaelshipman, 2023-12-23:
I2C should now be good to go as well, also changed address to `0x42`

```
const uint8_t ubx_cfg_prt_i2c_ubx_only[28] = {
        0xB5, 0x62, 0x06, 0x00, 0x14, 0x00, 0x00, 0x00, 0x00, 0x00,
        0x84, 0x00, 0x00, 0x00, 0x00, 0x00, 0x00, 0x00, 0x01, 0x00,
        0x01, 0x00, 0x00, 0x00, 0x00, 0x00, 0xA0, 0x96};  // sets I2C to UBX
                                                          // only, also sets I2C
                                                          // address to 0x42
```

michaelshipman, 2023-12-23:
ok well the address change definitely didn't work, still at `0x0F`

Moreover I don't get a UBX ack over i2c, just a whole lot of crap
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
michaelshipman, 2024-01-27:
Ok so I'm fairly certain that the GPS module that I was testing with over break had borked I2C (it was a random one I found in the lab)

Now working with the GPS on the BITSv5 boar the I2C comms are behaving as I would expect them to (proper 0xFF read)

Looks like it has been automatically configured to report some NMEA messages every second or so, will need to disable those and then figure out what UBX messages I want and write parsers for them.

michaelshipman, 2024-02-09:
Maybe I don't have to do all the parsing myself

https://github.com/u-blox/ubxlib

https://github.com/jacketizer/libnmea

That should make this whole thing a lot faster

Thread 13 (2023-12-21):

Iridium RP2040 Driver

michaelshipman, 2023-12-21:

michaelshipman, 2023-12-21:
Hopefully actually super simple looking at it

https://learn.adafruit.com/using-the-rockblock-iridium-modem?view=all

I guess you just spit a string over UART and then parse the string that you get back

michaelshipman, 2024-02-09:
Libraries also exist for this but I find them less promising. With any luck this can also be fast to implement

michaelshipman, 2024-03-25:
wrote something that I think can minimally work

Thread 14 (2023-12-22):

pressure temperature RP2040 driver

michaelshipman, 2023-12-22:

michaelshipman, 2023-12-22:
Ok so first pass at this is done, it compiles but who knows if it actually works and I'm not testing it rn, I have the SLAPS-SH board with me so maybe tomorrow I'll test it with actual hardware

https://github.com/UMDBPP/rp2040-ms5607-lib

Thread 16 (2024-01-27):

I2C Bus getting stuck

michaelshipman, 2024-01-27:
BITSv5 I2C bus appears to be stuck no matter what I do (both SDA and SCL ~2-3 volts)

michaelshipman, 2024-01-27:
Tried combinations of on board pull ups and RP2040 internal pull-ups, no fixes, did realize that we should only have 1 set of pull-ups on the board so I'm leaving the ones by the temp sensor off and keeping the ones by the GPS

michaelshipman, 2024-01-27:
Removed the GPS from the board and that appears to be what was causing the issues

Noticed potentially excess solder paste when pulling the GPS off so I'm going to clean that up and replace the GPS and see if that fixes the issue

michaelshipman, 2024-01-27:
seems that excess solder paste was the issue (a short somewhere)

GPS now detected at 0x42 (temp sensor at 0x77 btw)

also replaced GPS battery and everything is all good

Closed 2024-01-27.

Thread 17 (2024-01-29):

BITSv5 GPS troubleshooting

michaelshipman, 2024-01-29:
working on troubleshooting the GPS, so far it appears to sometimes see 2-3 satellites for a few minutes but never gets a lock. No changes have been made to the GPS's defaults yet. Below are log captures from the GPS while trying to get a lock.

[CoolTerm Capture 2024-01-28 16-57-20.txt](https://github.com/UMDBPP/command_module/files/14078440/CoolTerm.Capture.2024-01-28.16-57-20.txt)
[CoolTerm Capture 2024-01-27 18-01-10.txt](https://github.com/UMDBPP/command_module/files/14078441/CoolTerm.Capture.2024-01-27.18-01-10.txt)

michaelshipman, 2024-01-29:
Antenna datasheet

https://www.johansontechnology.com/datasheets/1575AT43A0040/1575AT43A0040.pdf

michaelshipman, 2024-01-29:
The antenna is supposed to be corner or end mounted.

Current idea is to rotate it 90° and see what happens

Board should get rev for either corner mount or a u.FL antenna

michaelshipman, 2024-01-29:
hook up a GPS antenna to the spectrum analyzer and see if there is anything nasty coming from BITS?

michaelshipman, 2024-01-31:
This was the spectrum I got from the GPS while sitting in my apartment

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

michaelshipman, 2024-01-31:
spectrum analyzer reference: https://portal.u-blox.com/s/question/0D52p00009XdiLGCAZ/has-zedf9p-an-available-spectrum-analyzer-ubxmonspan-message-cant-be-activated

michaelshipman, 2024-01-31:
changes needed for BITSv5.1
- expose GPS UART so I don't have to bodge to connect to u-center
- TIMEPULSE and EXTINT connected to GPIO
- antenna changes

michaelshipman, 2024-02-13:
Tested GPS on BITSV5.1 board with only GPS, Antenna, and decoupling cap on the board.

Easily got lock in way under a minute with 9 sats in view.

michaelshipman, 2024-02-18:
on to 5.2

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

Power changed and GPS is now on opposite side of the board from the radio and using a u.Fl connector so I can use the spectrum analyzer.

Also I realized that I may have been accidentally booting the GPS into safeboot so I've changed the GPIO assignments to make sure that doesn't happen, could have been the issue.

michaelshipman, 2024-03-02:
GPS on BITSv5.2 (without LoRa radio) successfully acquires lock after roughly 3 minutes from cold start.

- I have not populated the LoRa radio on this board yet, hopefully the fact that it is on the other side of the board from the GPS will mean it's not an issue.
- Not sure about any of the details of the gps patch used, just something I found in the lab luckily.

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

[CoolTerm Capture 2024-03-02 00-03-46.txt](https://github.com/UMDBPP/command_module/files/14468196/CoolTerm.Capture.2024-03-02.00-03-46.txt)

michaelshipman, 2024-03-03:
Locking in like a minute and a half today with the radio on the board. Had to futz with it a bit so only tested outside right now with the radio permanently in reset. Also notably the radio is refusing the work right now with status `aa` and errors `20` which indicates an XOSC error, hopefully as simple as needing a longer start time for the XOSC but I'm also worried that the specific radio that I am trying to use is broken since I think I exceeded the max voltage input on it accidentally when testing BITSv5.1 so may need to swap it out.

[CoolTerm Capture 2024-03-02 17-01-38.txt](https://github.com/UMDBPP/command_module/files/14471820/CoolTerm.Capture.2024-03-02.17-01-38.txt)
[CoolTerm Capture 2024-03-02 16-58-54.txt](https://github.com/UMDBPP/command_module/files/14471821/CoolTerm.Capture.2024-03-02.16-58-54.txt)

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

michaelshipman, 2024-03-04:
GPS and radio tested and work concurrently on BITSv5.2. Weird USB power issue currently but problem for a different issue!

Closing this as it seems to be solved.

michaelshipman, 2024-03-04:
I should add that the issue was not asserting the radio RST pin high before initializing it...duh

Closed 2024-03-04.

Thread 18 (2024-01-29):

BITSv5 GPS improvements

michaelshipman, 2024-01-29:
Need the following improvements to the design

- Re-positioned antenna
- TX_READY pin connected to GPIO
- EXTINT pin connected to GPIO
- Access to LNA_EN pin
- Break out the UART from the GPS to something I can solder to or better yet a connector of some kind (easily allows me to connect the GPS to u-center)

Closed 2024-02-01.

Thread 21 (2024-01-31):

change GPS antenna

michaelshipman, 2024-01-31:
need to either move the chip antenna to corner mount or change to ufl, concerned that current reception with the chip antenna is poor

michaelshipman, 2024-01-31:
Will try to keep chip, just need to conform to spec below

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

michaelshipman, 2024-02-01:
both chip antennas have been replaced by ufl connectors

maybe we can go back to chips later but this is safer for now

Closed 2024-02-01.

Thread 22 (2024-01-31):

fix battery connector polarity

michaelshipman, 2024-01-31:

michaelshipman, 2024-02-01:
has been flipped now

Closed 2024-02-01.

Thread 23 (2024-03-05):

Smaller RP2040 Flash IC

michaelshipman, 2024-03-05:
Turns out the Pico uses a 16MB chip with a smaller area than we have been using. Easy way to save space since that flash IC is one of the biggest things on the board right now.

https://www.digikey.com/en/products/detail/winbond-electronics/W25Q16JVUXIQ-TR/15182017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

michaelshipman, 2024-03-18:
JJ pointed out that this is a 2 megabyte chip not a 16 megabyte, if not using for data storage it would be perfectly adequate

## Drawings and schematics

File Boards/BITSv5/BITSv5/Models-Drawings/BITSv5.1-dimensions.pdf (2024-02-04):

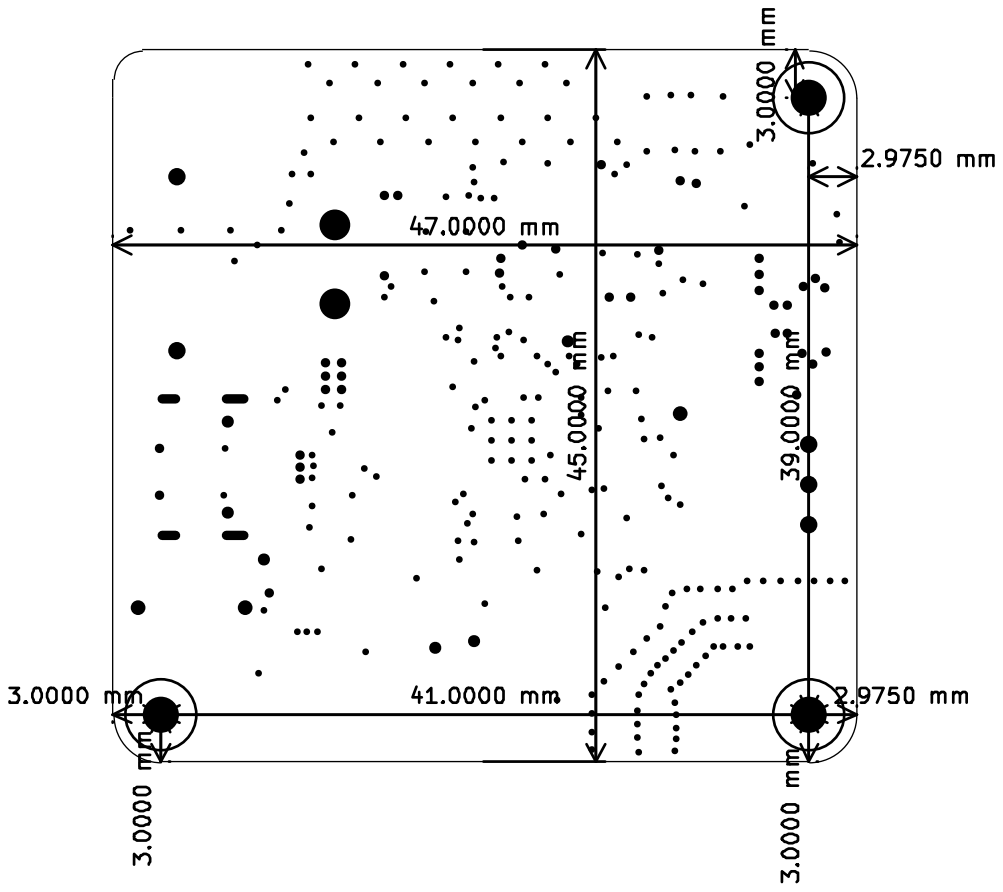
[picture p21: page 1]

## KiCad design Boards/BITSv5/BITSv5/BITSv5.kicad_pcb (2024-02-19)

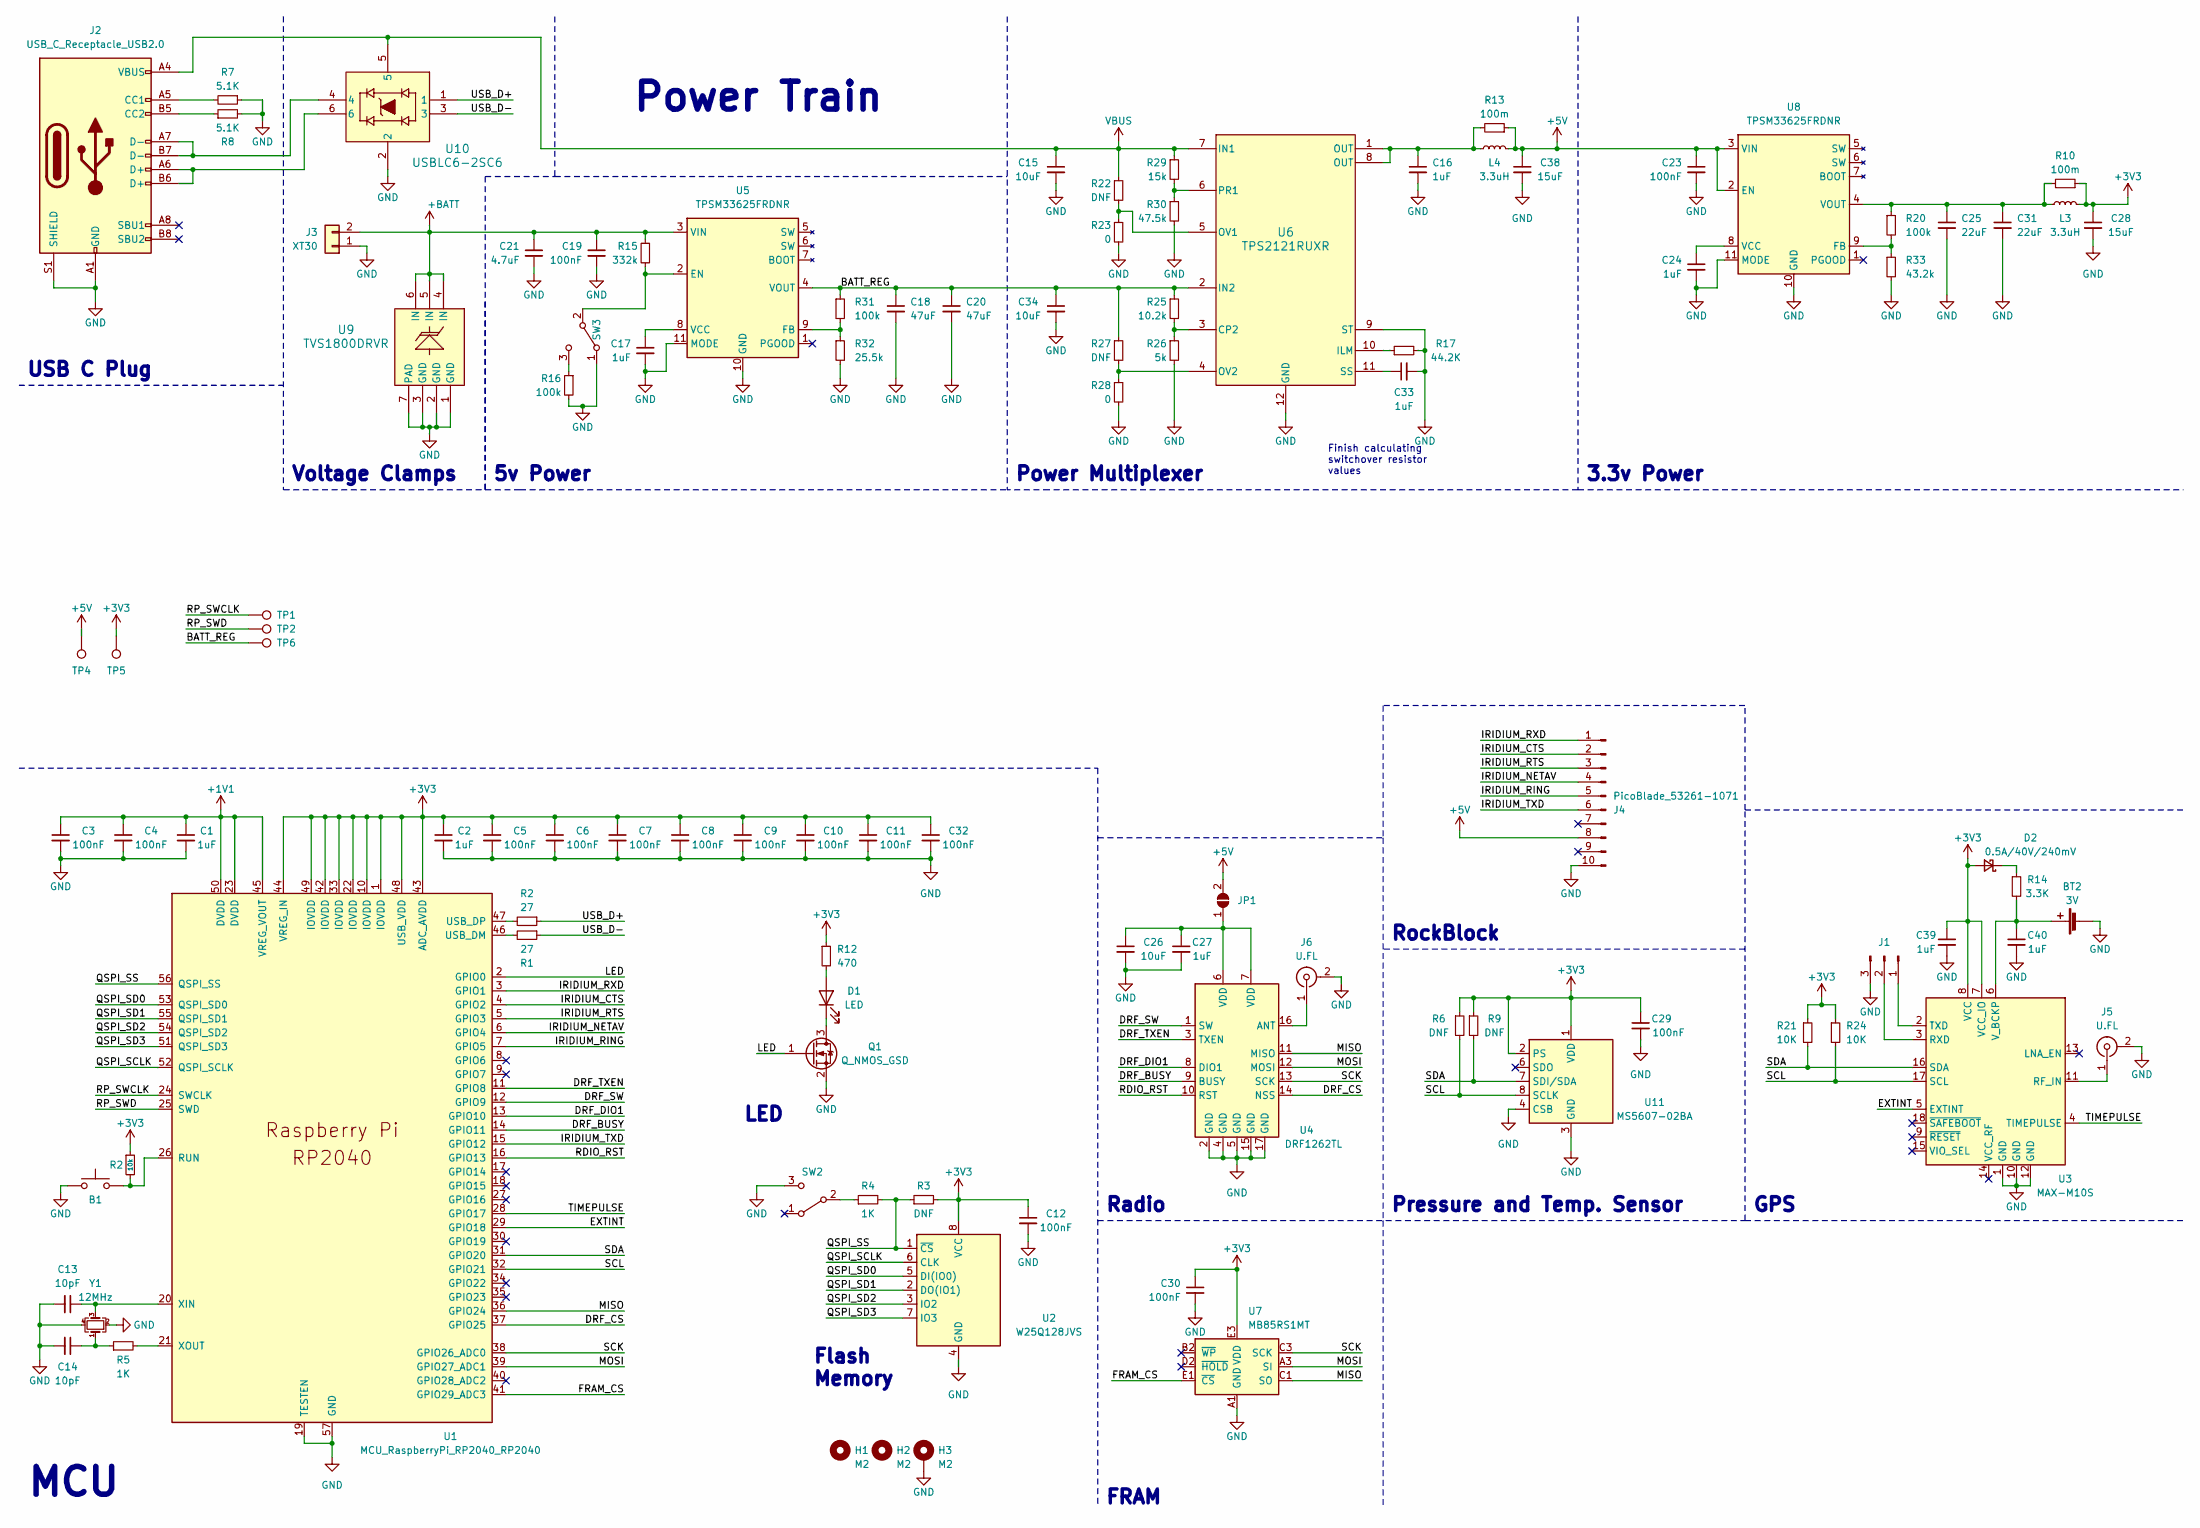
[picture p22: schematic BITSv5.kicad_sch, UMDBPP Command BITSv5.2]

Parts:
B1: KMR2; SW_Push_1P1T_NO_CK_KMR2
BT2: 3V; SEIKO_ML414H_IV01E
C1, C2: 1uF; C_0402_1005Metric
C3, C4, C5, C6, C7, C8, C9, C10, C11, C12, C32: 100nF; C_0402_1005Metric
C13, C14: 10pF; C_0402_1005Metric
C15, C26, C34: 10uF; C_0603_1608Metric
C16, C17, C24, C27, C33, C39, C40: 1uF; C_0603_1608Metric
C18, C20: 47uF; C_1206_3216Metric
C19, C23, C29, C30: 100nF; C_0603_1608Metric
C21: 4.7uF; C_0805_2012Metric
C25, C31: 22uF; C_0805_2012Metric
C28, C38: 15uF; C_1206_3216Metric
D1: LED; LED_0603_1608Metric
D2: 0.5A/40V/240mV; D_SOD-123F
H1, H2, H3: M2; MountingHole_2.2mm_M2_Pad
J1: Conn_01x03_Pin; PinHeader_1x03_P2.54mm_Vertical
J2: USB_C_Receptacle_USB2.0; USB_C_Receptacle_GCT_USB4105-xx-A_16P_TopMnt_Horizontal
J3: XT30; AMASS_XT30PW-M_1x02_P2.50mm_Horizontal
J4: PicoBlade_53261-1071; Molex_PicoBlade_53261-1071_1x10-1MP_P1.25mm_Horizontal
J5, J6: U.FL; U.FL_Molex_MCRF_73412-0110_Vertical
JP1: SolderJumper_2_Open; SolderJumper-2_P1.3mm_Open_RoundedPad1.0x1.5mm
L3, L4: 3.3uH; L_1210_3225Metric
Q1: Q_NMOS_GSD; SOT-23-3
R1: 27; R_0402_1005Metric
R2: 10k; R_0603_1608Metric
R3, R6, R9, R22, R27: DNF; R_0603_1608Metric
R4: 1K; R_0603_1608Metric
R5: 1K; R_0402_1005Metric
R7, R8: 5.1K; R_0603_1608Metric_Pad0.98x0.95mm_HandSolder
R10, R13: 100m; R_0603_1608Metric
R12: 470; R_0603_1608Metric
R14: 3.3K; R_0603_1608Metric
R15: 332k; R_0603_1608Metric
R16, R20, R31: 100k; R_0603_1608Metric
R17: 44.2K; R_0603_1608Metric
R21, R24: 10K; R_0603_1608Metric
R23, R28: 0; R_0603_1608Metric
R25: 10.2k; R_0603_1608Metric
R26: 5k; R_0603_1608Metric
R29: 15k; R_0603_1608Metric
R30: 47.5k; R_0603_1608Metric
R32: 25.5k; R_0603_1608Metric
R33: 43.2k; R_0603_1608Metric
SW2: CAS-120TB_NDC-M
SW3: SLIDE; CL-SB-12B-01_NDC
TP1, TP2: TestPoint; TestPoint_Pad_D2.0mm
TP4, TP5, TP6: TestPoint; TestPoint_Keystone_5000-5004_Miniature
U1: MCU_RaspberryPi_RP2040_RP2040; RP2040-QFN-56
U2: W25Q128JVS; WSON_128JVPIQ_WIN
U3: MAX-M10S; ublox_MAX
U4: DRF1262TL
U5, U8: TPSM33625FRDNR; RDN0011A-MFG-NO-VIA
U6: TPS2121RUXR; TPS2121
U7: MB85RS1MT; BGA8CP30X40_5X3_309X228X35B25N
U9: TVS1800DRVR; TVS1800
U10: USBLC6-2SC6; SOT23-6L_STM
U11: MS5607-02BA; LGA-8_3x5mm_P1.25mm
Y1: 12MHz; Crystal_SMD_2520-4Pin_2.5x2.0mm

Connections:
+1V1: C1.1, C3.1, C4.1, U1.23 (DVDD), U1.45 (VREG_VOUT), U1.50 (DVDD)
+5V: C23.1, C38.1, J4.8, JP1.2 (B), L4.1, R13.1, TP4.1, U8.2 (EN), U8.3 (VIN)
+BATT: C19.1, C21.1, J3.2, R15.1, U5.3 (VIN), U9.4 (IN), U9.5 (IN), U9.6 (IN)
/BATT_REG: C18.1, C20.1, C34.1, R25.1, R27.1, R31.1, TP6.1, U5.4 (VOUT), U6.2 (IN2)
/DRF_BUSY: U1.14 (GPIO11), U4.9 (BUSY)
/DRF_CS: U1.37 (GPIO25), U4.14 (NSS)
/DRF_DIO1: U1.13 (GPIO10), U4.8 (DIO1)
/DRF_SW: U1.12 (GPIO9), U4.1 (SW)
/DRF_TXEN: U1.11 (GPIO8), U4.3 (TXEN)
/EXTINT: U1.29 (GPIO18), U3.5 (EXTINT)
/FRAM_CS: U1.41 (GPIO29_ADC3), U7.E1 (~CS)
/IRIDIUM_CTS: J4.2, U1.4 (GPIO2)
/IRIDIUM_NETAV: J4.4, U1.6 (GPIO4)
/IRIDIUM_RING: J4.5, U1.7 (GPIO5)
/IRIDIUM_RTS: J4.3, U1.5 (GPIO3)
/IRIDIUM_RXD: J4.1, U1.3 (GPIO1)
/IRIDIUM_TXD: J4.6, U1.15 (GPIO12)
/LED: Q1.1 (G), U1.2 (GPIO0)
/MISO: U1.36 (GPIO24), U4.11 (MISO), U7.C1 (SO)
/MOSI: U1.39 (GPIO27_ADC1), U4.12 (MOSI), U7.A3 (SI)
/QSPI_SCLK: U1.52 (QSPI_SCLK), U2.6 (CLK)
/QSPI_SD0: U1.53 (QSPI_SD0), U2.5 (DI(IO0))
/QSPI_SD1: U1.55 (QSPI_SD1), U2.2 (DO(IO1))
/QSPI_SD2: U1.54 (QSPI_SD2), U2.3 (IO2)
/QSPI_SD3: U1.51 (QSPI_SD3), U2.7 (IO3)
/QSPI_SS: R3.1, R4.2, U1.56 (QSPI_SS), U2.1 (~CS)
/RDIO_RST: U1.16 (GPIO13), U4.10 (RST)
/RP_SWCLK: TP1.1, U1.24 (SWCLK)
/RP_SWD: TP2.1, U1.25 (SWD)
/SCK: U1.38 (GPIO26_ADC0), U4.13 (SCK), U7.C3 (SCK)
/SCL: R6.2, R24.2, U1.32 (GPIO21), U3.17 (SCL), U11.8 (SCLK)
/SDA: R9.2, R21.2, U1.31 (GPIO20), U3.16 (SDA), U11.7 (SDI/SDA)
/TIMEPULSE: U1.28 (GPIO17), U3.4 (TIMEPULSE)
/USB_D-: R1.1, U10.3
unnamed: BT2.1 (+), C40.1, R14.2, U3.6 (V_BCKP)
unnamed: C14.1, R5.1, Y1.1
unnamed: C16.1, L4.2, R13.2, U6.1 (OUT), U6.8 (OUT)
unnamed: D1.2 (A), R12.2
unnamed: D1.1 (K), Q1.3 (D)
unnamed: D2.1 (K), R14.1
unnamed: J1.1, U3.2 (TXD)
unnamed: J1.2, U3.3 (RXD)
unnamed: J2.A5 (CC1), R7.2
unnamed: J2.B5 (CC2), R8.1
unnamed: J2.A6 (D+), J2.B6 (D+), U10.6
unnamed: J2.A7 (D-), J2.B7 (D-), U10.4
unnamed: J5.1 (In), U3.11 (RF_IN)
unnamed: J6.1 (In), U4.16 (ANT)
unnamed: C26.1, C27.1, JP1.1 (A), U4.6 (VDD), U4.7 (VDD)
unnamed: R4.1, SW2.2 (B)
unnamed: R15.2, SW3.2 (B), U5.2 (EN)
unnamed: R16.1, SW3.3 (C)
unnamed: R1.2, U1.46 (USB_DM)
unnamed: C13.1, U1.20 (XIN), Y1.3
unnamed: R5.2, U1.21 (XOUT)
unnamed: R31.2, R32.1, U5.9 (FB)
unnamed: C17.1, U5.8 (VCC)
unnamed: R25.2, R26.1, U6.3 (CP2)
unnamed: R17.1, U6.10 (ILM)
unnamed: R22.2, R23.1, U6.5 (OV1)
unnamed: R27.2, R28.1, U6.4 (OV2)
unnamed: R29.2, R30.1, U6.6 (PR1)
unnamed: C33.1, U6.11 (SS)
unnamed: R20.2, R33.1, U8.9 (FB)
unnamed: C24.1, U8.8 (VCC)
unnamed: C25.1, C31.1, L3.2, R10.2, R20.1, U8.4 (VOUT)
VBUS: C15.1, J2.A4 (VBUS), J2.A9 (VBUS), J2.B4 (VBUS), J2.B9 (VBUS), R22.1, R29.1, U6.7 (IN1), U10.5

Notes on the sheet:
Pressure and Temp. Sensor
Power Train
USB C Plug
FRAM
3.3v Power
Finish calculating switchover resistor values
GPS
Power Multiplexer
LED
RockBlock
Voltage Clamps
Flash Memory
MCU
Radio
5v Power

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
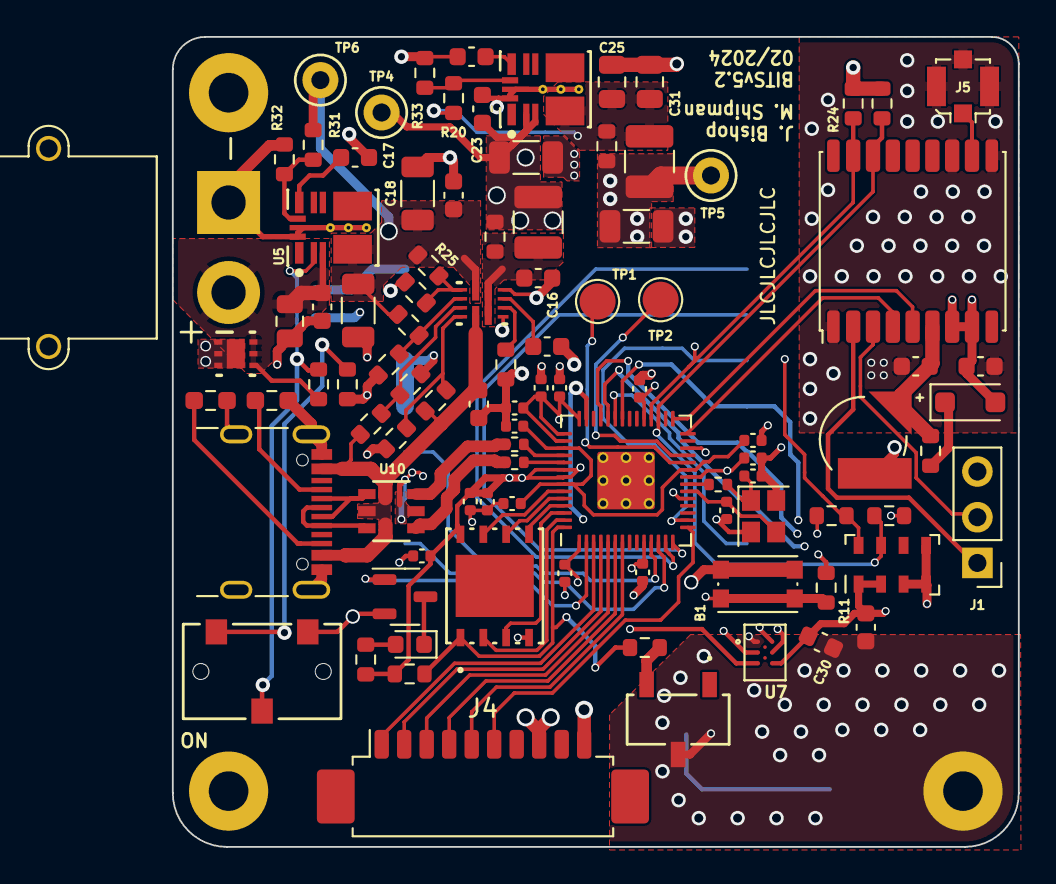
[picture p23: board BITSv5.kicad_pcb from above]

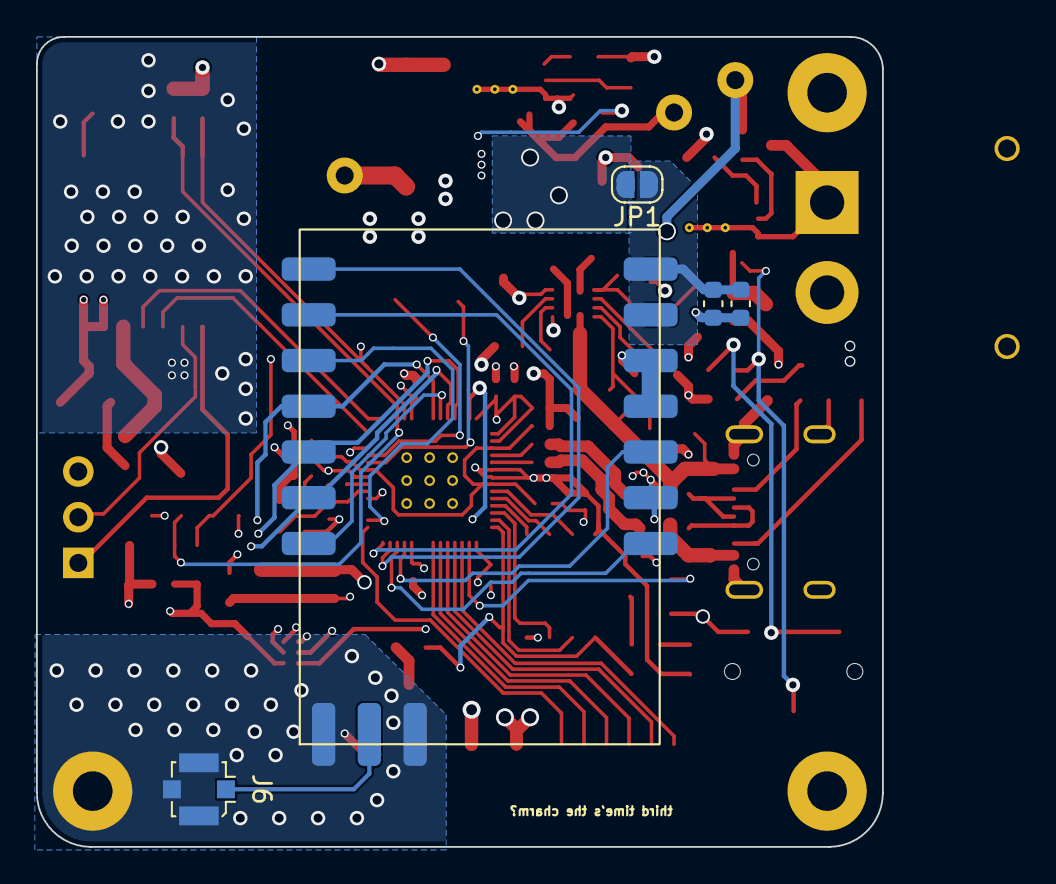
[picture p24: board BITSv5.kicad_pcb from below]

Board: 4 copper layers, 47.0 x 45.0 mm, 103 parts (5 on the bottom side), 72 nets.

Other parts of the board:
R11: 10k; R_0603_1608Metric

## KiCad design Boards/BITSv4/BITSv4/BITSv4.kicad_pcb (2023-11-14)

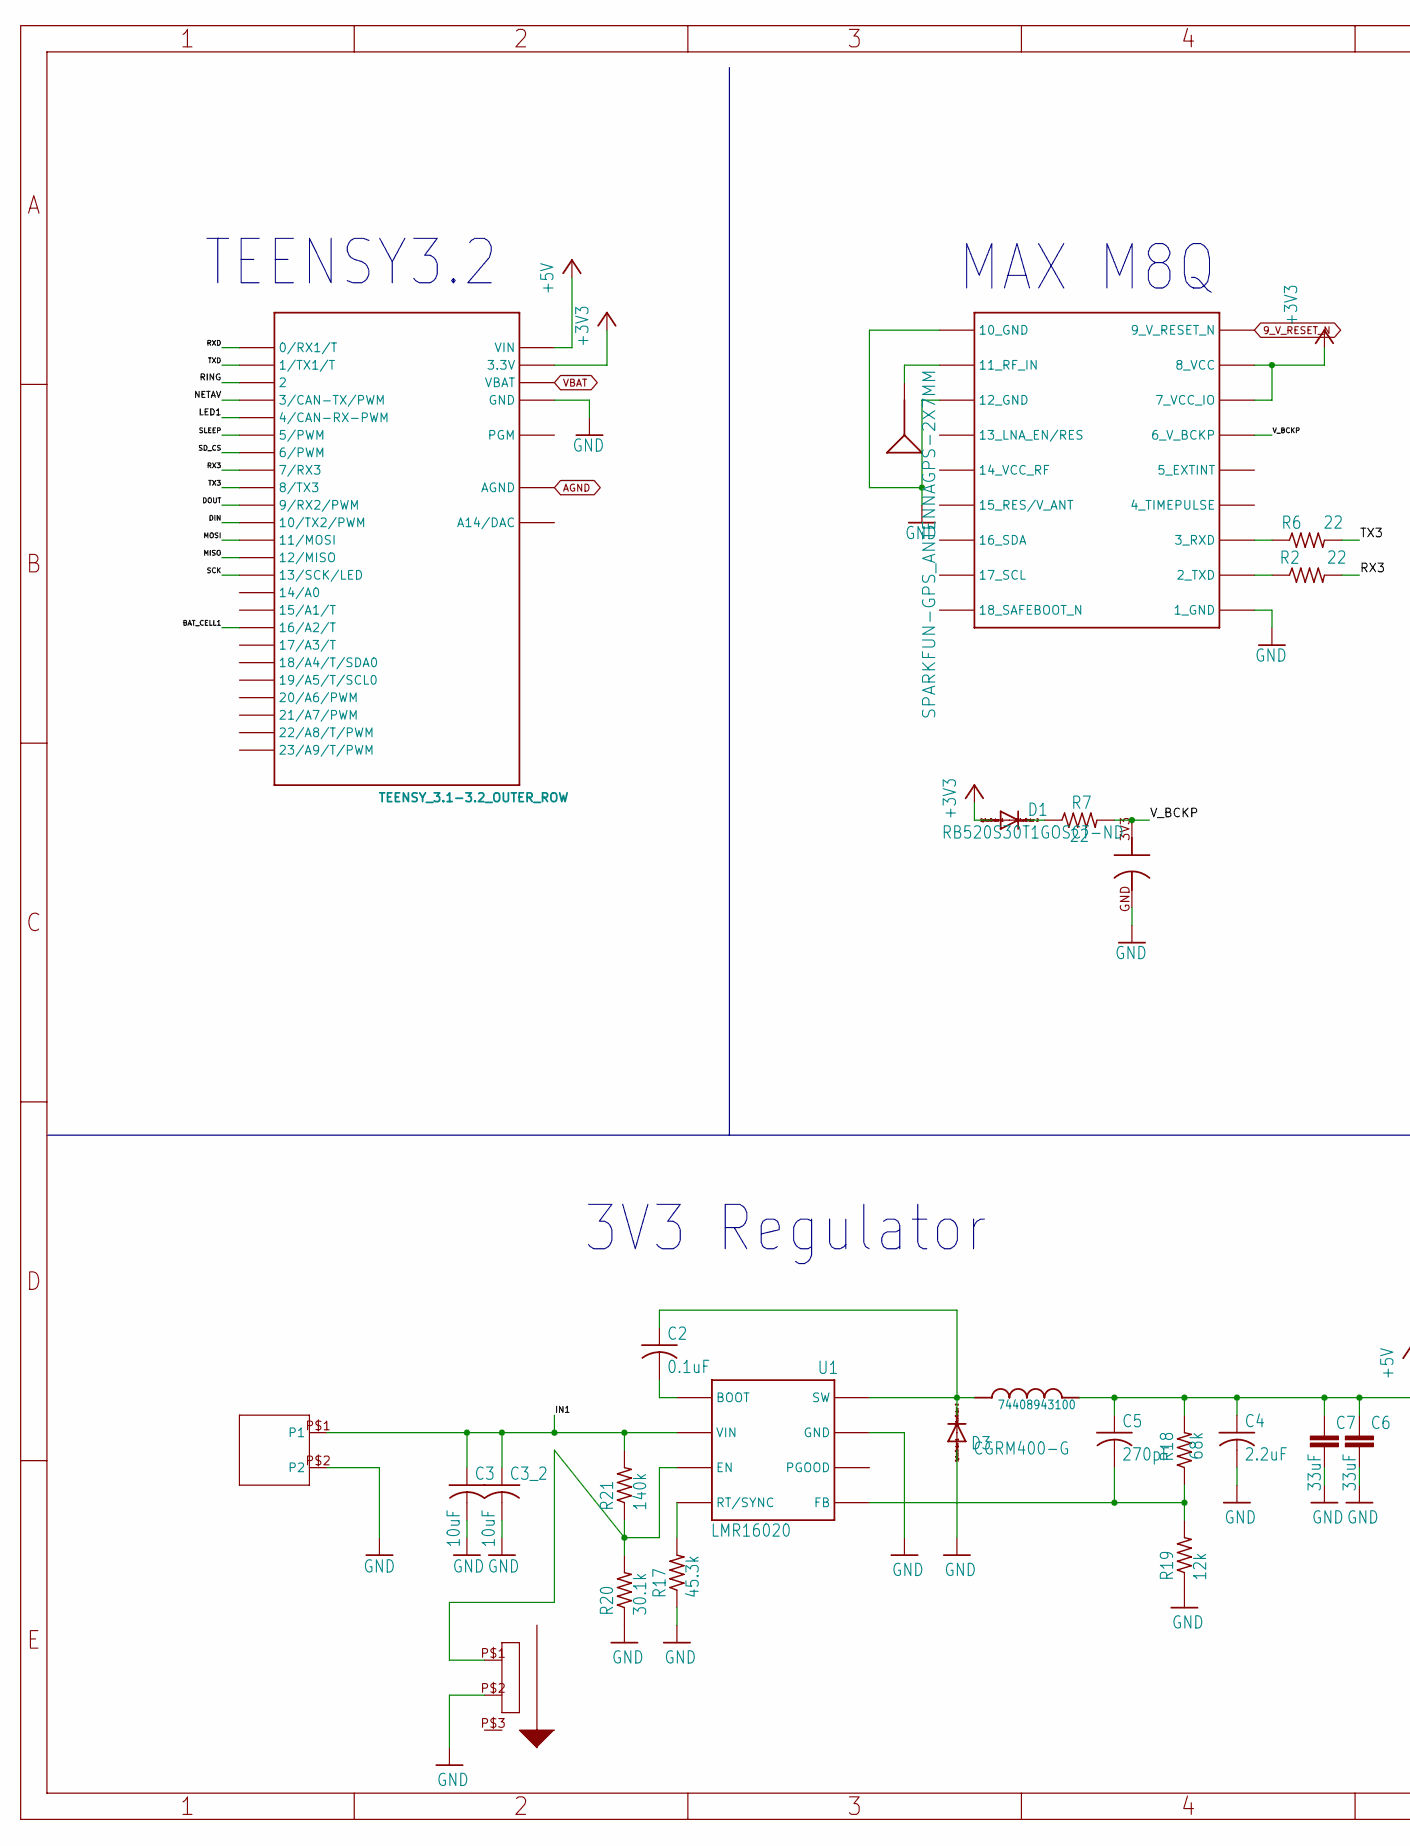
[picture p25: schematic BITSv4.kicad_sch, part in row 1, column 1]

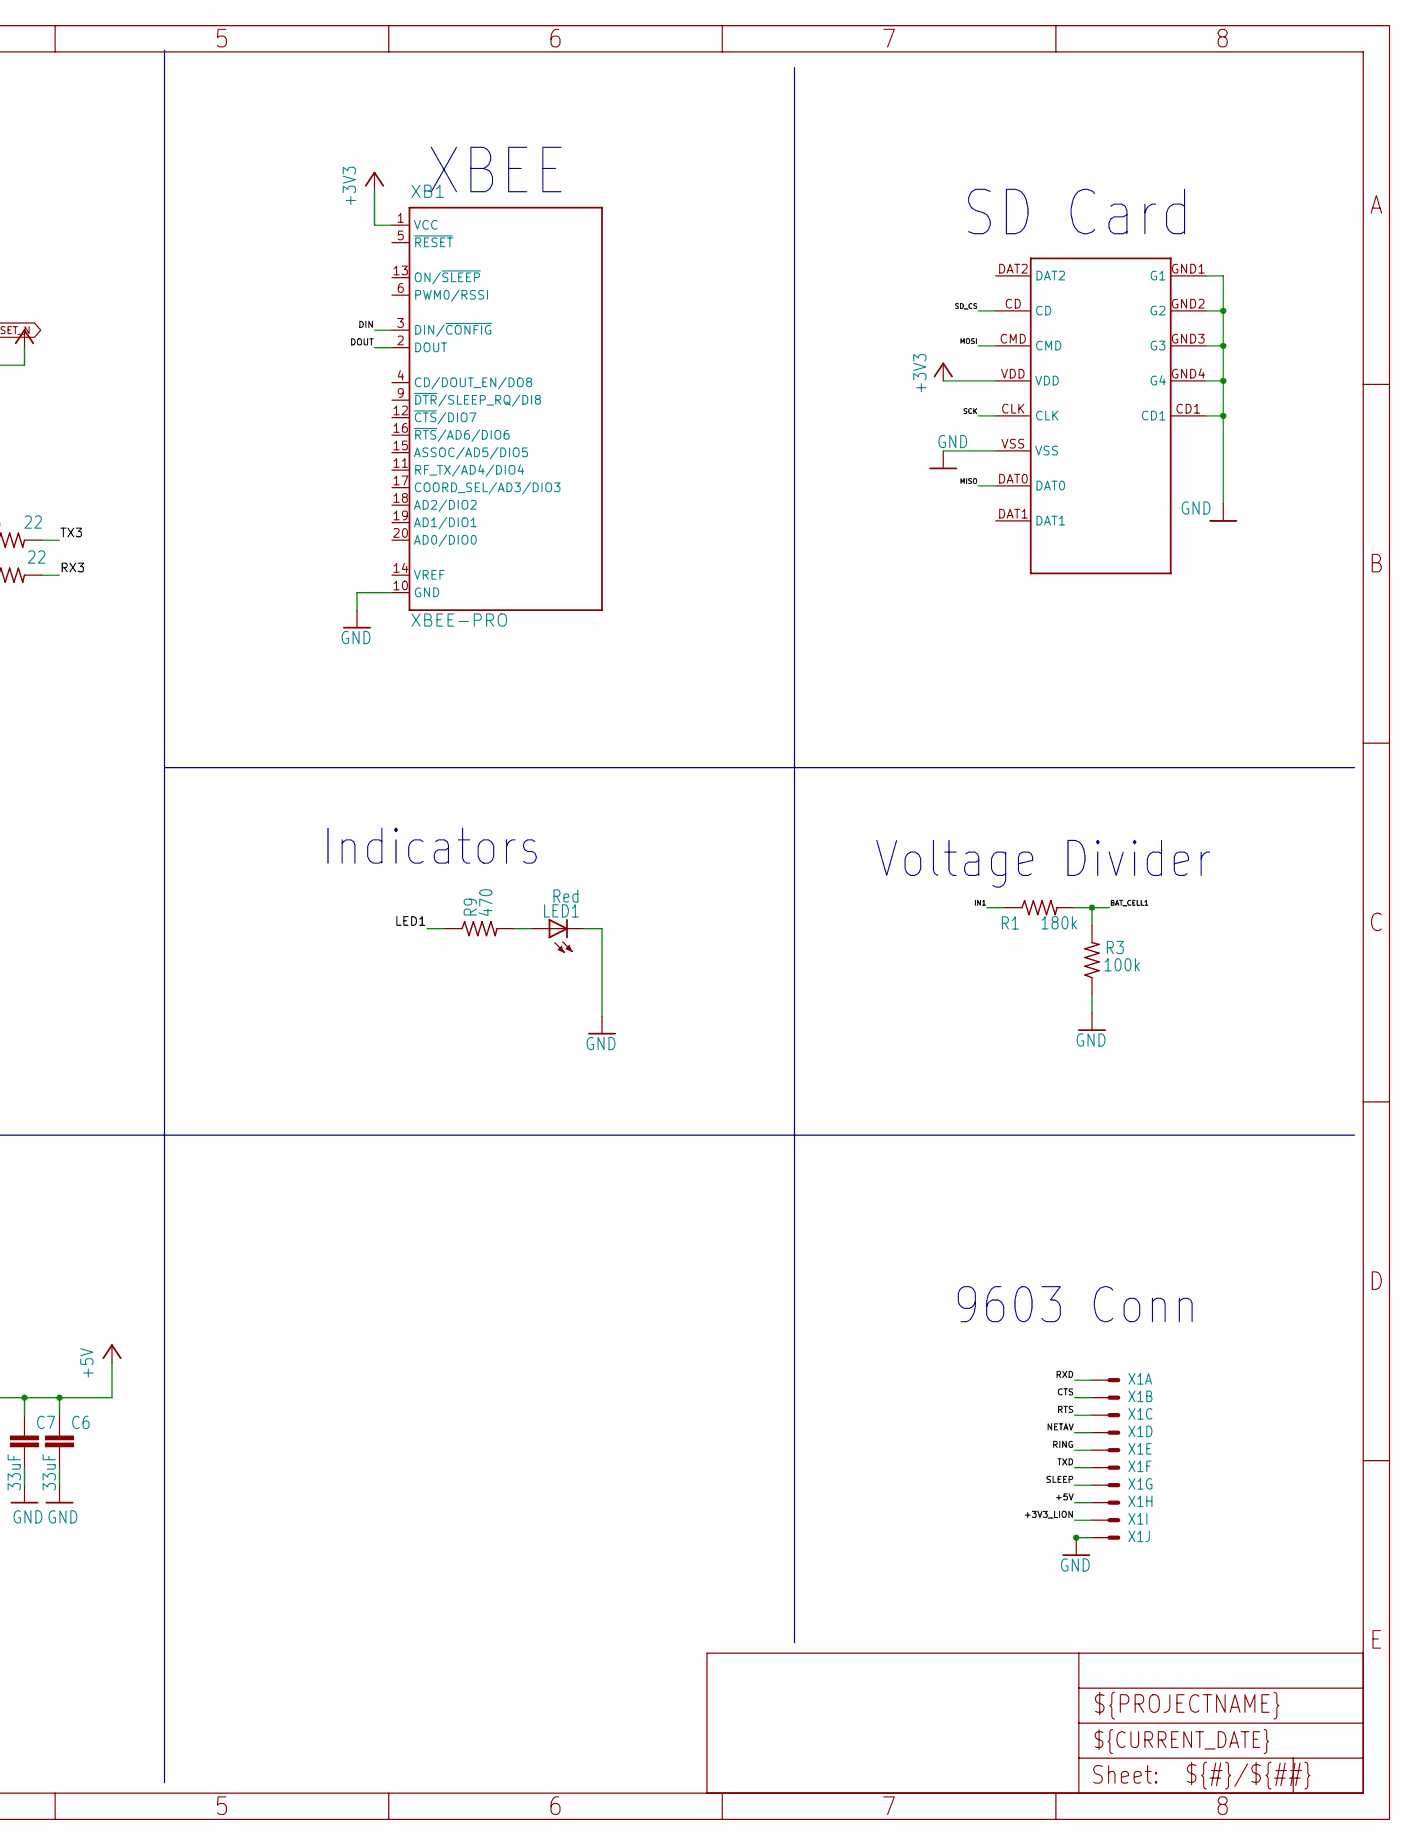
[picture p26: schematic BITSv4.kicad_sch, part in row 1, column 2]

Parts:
C1: 0.2F; ELNASUPERCAP
C2: 0.1uF; C0603
C3, C3_2: 10uF; C0805
C4: 2.2uF; C0603
C5: 270pF; C0402
C6, C7: 33uF; C050-024X044
D1: RB520S30T1GOSCT-ND; SOD523
D3: CGRM400-G; SOD-123_MINI-SMA
L1: 74408943100
LED1: Red; CHIP-LED0603
R1: 180k; R0603
R2, R6, R7: 22; R0603
R3: 100k; R0603
R9: 470; R0603
R17: 45.3k; R0603
R18: 68k; R0603
R19: 12k; R0603
R20: 30.1k; R0603
R21: 140k; R0603
U1: LMR16020; SO8
U$1: 559350210
U$2: TEENSY_3.1-3.2_OUTER_ROW; TEENSY_3.0-3.2&LC_OUTER_ROW
U$3: CL-SB-12B-01
U$4: MICRO_SD; MICRO_SD_HINGED
U$7: MAX-M8
U$8: SPARKFUN-GPS_ANTENNAGPS-2X7MM; SPARKFUN-GPS_ANT-GPS-2X7MM
X1: 53?-10261; 53261-10
XB1: XBEE-PRO

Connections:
9_V_RESET_N: U$7.9_RESET_N (9_V_RESET_N)
+3V3: D1.A, U$2.3.3V, U$2.3.3V1 (3.3V), U$4.VDD, U$7.7_VCC_IO, U$7.8_VCC, XB1.1 (VCC)
+3V3_LION: X1.9
+5V: C4.1, C5.1, C6.1, C7.1, L1.P$2, R18.2, U$2.VIN, X1.8
AGND: U$2.AGND
BAT_CELL1: R1.2, R3.2, U$2.16/A2 (16/A2/T)
CTS: X1.2
DIN: U$2.10 (10/TX2/PWM), XB1.3 (DIN/~CONFIG)
DOUT: U$2.9 (9/RX2/PWM), XB1.2 (DOUT)
FB: C5.2, R18.1, R19.2, U1.P$5 (FB)
GND: C1.GND, C3.2, C3_2.2, C4.2, C6.2, C7.2, D3.A, LED1.C, R3.1, R17.1, R19.1, R20.1, U1.P$7 (GND), U1.PAD (GND), U$1.P$2 (P2), U$2.GND, U$2.GND1 (GND), U$3.P$2 (P2), U$4.CD1, U$4.GND1 (G1), U$4.GND2 (G2), U$4.GND3 (G3), U$4.GND4 (G4), U$4.VSS, U$7.1_GND, U$7.10_GND, U$7.12_GND, X1.10, XB1.10 (GND)
IN1: C3.1, C3_2.1, R1.1, R21.2, U1.P$2 (VIN), U$1.P$1 (P1)
LED1: R9.1, U$2.4 (4/CAN-RX-PWM)
MISO: U$2.12 (12/MISO), U$4.DAT0
MOSI: U$2.11 (11/MOSI), U$4.CMD
unnamed: U$7.11_RF_IN, U$8.1
unnamed: D1.C, R7.1
unnamed: R6.1, U$7.3_RXD
unnamed: R2.1, U$7.2_TXD
unnamed: LED1.A, R9.2
unnamed: R20.2, R21.1, U1.P$3 (EN), U$3.P$1 (P1)
unnamed: R17.2, U1.P$4 (RT/SYNC)
unnamed: C2.2, U1.P$1 (BOOT)
NETAV: U$2.3 (3/CAN-TX/PWM), X1.4
RING: U$2.2, X1.5
RTS: X1.3
RX3: R2.2, U$2.7 (7/RX3)
RXD: U$2.0 (0/RX1/T), X1.1
SCK: U$2.13 (13/SCK/LED), U$4.CLK
SD_CS: U$2.6 (6/PWM), U$4.CD
SLEEP: U$2.5 (5/PWM), X1.7
SW: C2.1, D3.C, L1.P$1, U1.P$8 (SW)
TX3: R6.2, U$2.8 (8/TX3)
TXD: U$2.1 (1/TX1/T), X1.6
VBAT: U$2.VBAT
V_BCKP: C1.3V3, R7.2, U$7.6_V_BCKP

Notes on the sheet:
SD Card
XBEE
Indicators
9603 Conn
3V3 Regulator
TEENSY3.2
MAX M8Q
Voltage Divider

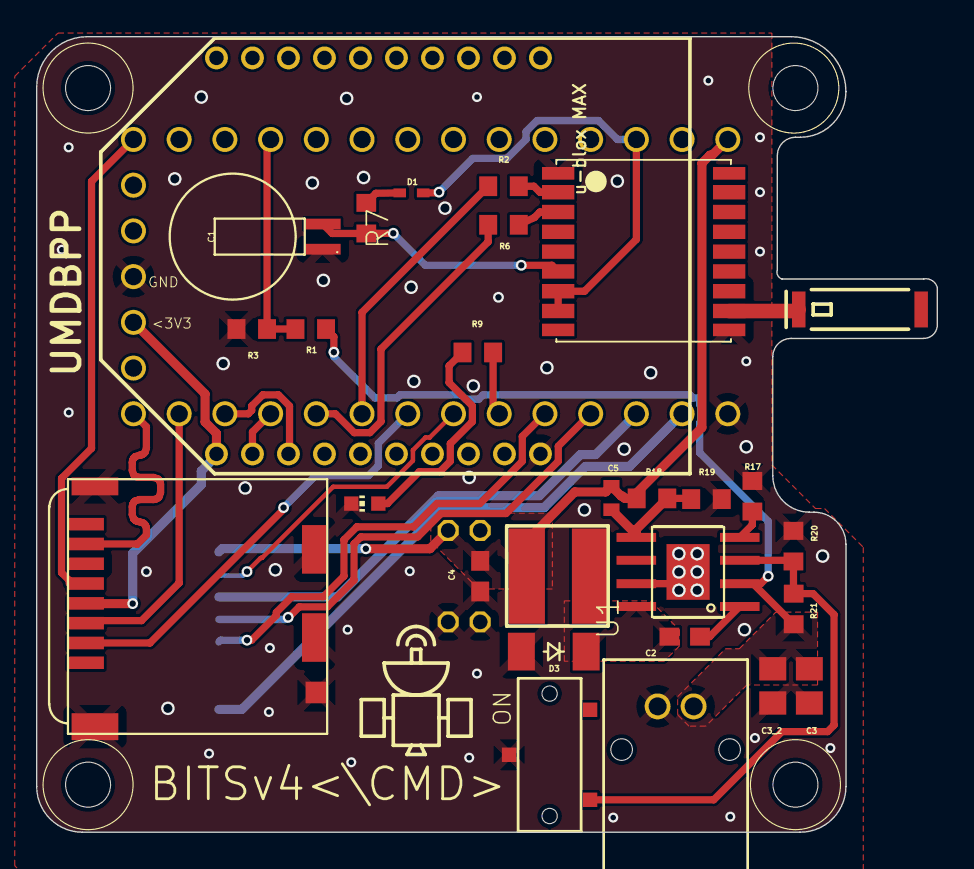
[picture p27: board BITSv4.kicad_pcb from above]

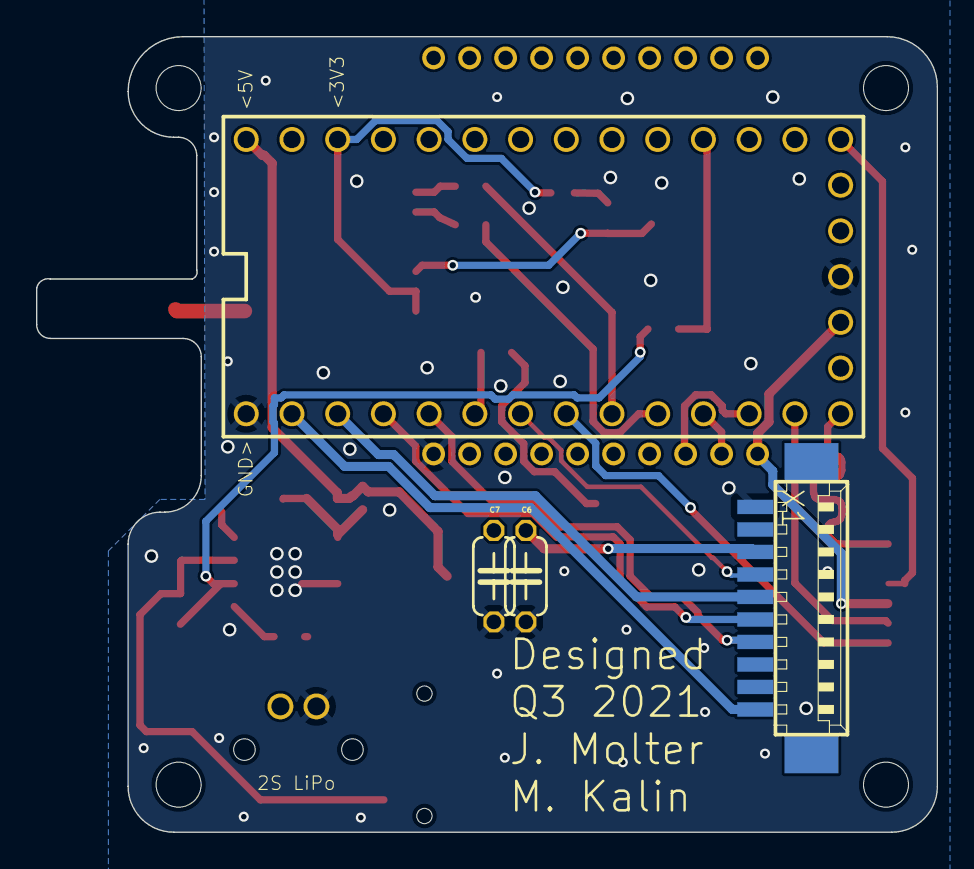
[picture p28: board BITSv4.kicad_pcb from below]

Board: 2 copper layers, 50.0 x 44.2 mm, 36 parts (4 on the bottom side), 30 nets.

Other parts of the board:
@HOLE0, @HOLE1, @HOLE2, @HOLE3: (no value)

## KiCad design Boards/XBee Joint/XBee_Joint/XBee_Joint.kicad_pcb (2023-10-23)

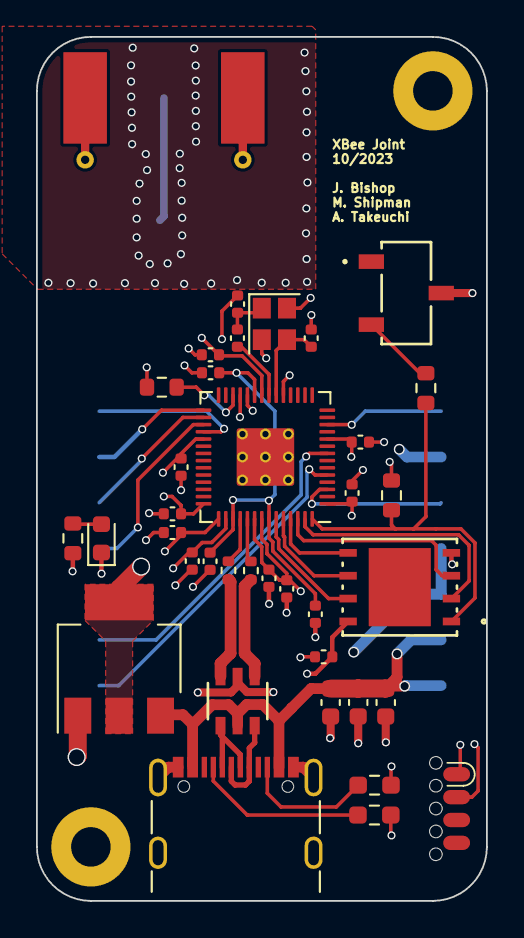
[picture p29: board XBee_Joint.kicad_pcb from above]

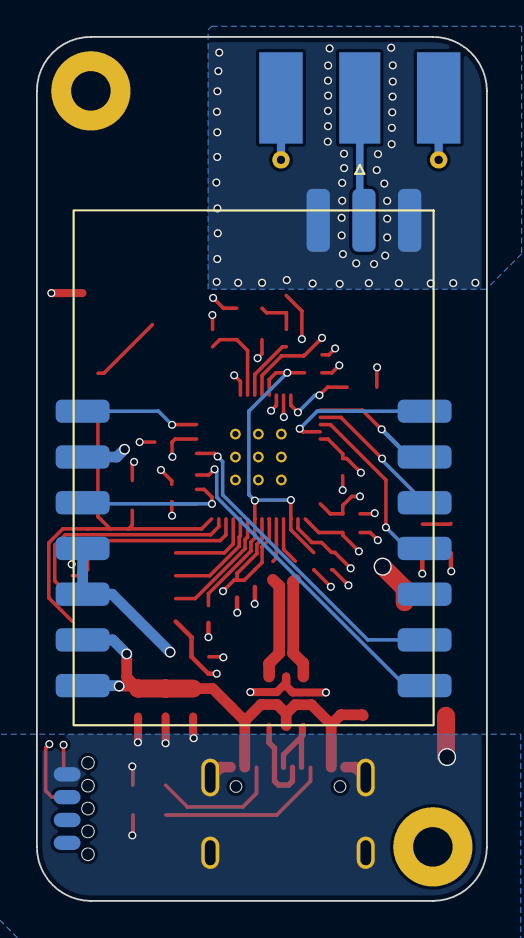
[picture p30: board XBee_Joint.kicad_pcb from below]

Board: 4 copper layers, 25.0 x 48.0 mm, 40 parts (2 on the bottom side), 35 nets.

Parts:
AE1: Antenna; SMA_Molex_73251-1153_EdgeMount_Horizontal
C1, C4, C7, C8, C9, C10, C11, C12, C13, C14, C15: 100nF; C_0402_1005Metric
C2, C3: 10pF; C_0402_1005Metric
C5, C6: 1uF; C_0402_1005Metric
C16: 1uF; C_0603_1608Metric
C17: 100nF; C_0603_1608Metric
C18: 10uF; C_0603_1608Metric
D1: LED; LED_0603_1608Metric
H1, H2: M2; MountingHole_2.2mm_M2_Pad
J1: SOICbite; SOIC_clipProgSmall
J2: USB_C_Receptacle_USB2.0; USB_C_Receptacle_GCT_USB4105-xx-A_16P_TopMnt_Horizontal
R1: 1K; C_0402_1005Metric
R2, R3: 27; R_0402_1005Metric
R4: 10K; R_0603_1608Metric
R6: 470; R_0603_1608Metric
R7: 1K; R_0603_1608Metric
R8: DNF; R_0603_1608Metric
R9, R10: 5.1K; R_0603_1608Metric_Pad0.98x0.95mm_HandSolder
SW2: CAS-120TB_NDC-M
U1: MCU_RaspberryPi_RP2040_RP2040; RP2040-QFN-56
U2: AP2114H-3.3TRG1; SOT-223-3_TabPin2
U3: DRF1262TL
U4: W25Q128JVS; WSON_128JVPIQ_WIN
U5: USBLC6-2SC6; SOT23-6L_STM
Y1: 12MHz; Crystal_SMD_2520-4Pin_2.5x2.0mm

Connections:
+1V1: C1.1, C4.1, C5.1, U1.23 (DVDD), U1.45 (VREG_VOUT), U1.50 (DVDD)
+3V3: C6.1, C7.1, C8.1, C9.1, C10.1, C11.1, C12.1, C13.1, C14.1, C15.1, R4.1, R6.1, R8.2, U1.1 (IOVDD), U1.10 (IOVDD), U1.22 (IOVDD), U1.33 (IOVDD), U1.42 (IOVDD), U1.43 (ADC_AVDD), U1.44 (VREG_IN), U1.48 (USB_VDD), U1.49 (IOVDD), U2.2 (VO), U4.8 (VCC)
/DRF_BUSY: U1.8 (GPIO6), U3.9 (BUSY)
/DRF_CLK: U1.29 (GPIO18), U3.13 (SCK)
/DRF_CS: U1.32 (GPIO21), U3.14 (NSS)
/DRF_DIO1: U1.5 (GPIO3), U3.8 (DIO1)
/DRF_MISO: U1.31 (GPIO20), U3.11 (MISO)
/DRF_MOSI: U1.30 (GPIO19), U3.12 (MOSI)
/DRF_SW: U1.12 (GPIO9), U3.1 (SW)
/DRF_TXEN: U1.3 (GPIO1), U3.3 (TXEN)
/QSPI_SCLK: U1.52 (QSPI_SCLK), U4.6 (CLK)
/QSPI_SD0: U1.53 (QSPI_SD0), U4.5 (DI(IO0))
/QSPI_SD1: U1.55 (QSPI_SD1), U4.2 (DO(IO1))
/QSPI_SD2: U1.54 (QSPI_SD2), U4.3 (IO2)
/QSPI_SD3: U1.51 (QSPI_SD3), U4.7 (IO3)
/QSPI_SS: R7.2, R8.1, U1.56 (QSPI_SS), U4.1 (~CS)
/RP_SWCLK: J1.1, U1.24 (SWCLK)
/RP_SWD: J1.2, U1.25 (SWD)
/USB_D+: R2.1, U5.1
/USB_D-: R3.1, U5.3
GND: C1.2, C2.2, C3.2, C4.2, C5.2, C6.2, C7.2, C8.2, C9.2, C10.2, C11.2, C12.2, C13.2, C14.2, C15.2, C16.2, C17.2, C18.2, D1.1 (K), J1.8, J2.A1 (GND), J2.A12 (GND), J2.B1 (GND), J2.B12 (GND), J2.S1 (SHIELD), R9.1, R10.2, SW2.3 (C), U1.19 (TESTEN), U1.57 (GND), U2.1 (GND), U3.2 (GND), U3.4 (GND), U3.5 (GND), U3.15 (GND), U3.17 (GND), U4.4 (GND), U5.2, Y1.2, Y1.4
unnamed: AE1.1 (A), U3.16 (ANT)
unnamed: C3.1, R1.1, Y1.1
unnamed: D1.2 (A), R6.2
unnamed: J2.A5 (CC1), R9.2
unnamed: J2.B5 (CC2), R10.1
unnamed: J2.A6 (D+), J2.B6 (D+), U5.6
unnamed: J2.A7 (D-), J2.B7 (D-), U5.4
unnamed: R7.1, SW2.2 (B)
unnamed: R4.2, U1.26 (RUN)
unnamed: R3.2, U1.46 (USB_DM)
unnamed: R2.2, U1.47 (USB_DP)
unnamed: C2.1, U1.20 (XIN), Y1.3
unnamed: R1.2, U1.21 (XOUT)
VBUS: C16.1, C17.1, C18.1, J2.A4 (VBUS), J2.A9 (VBUS), J2.B4 (VBUS), J2.B9 (VBUS), U2.3 (VI), U3.6 (VDD), U3.7 (VDD), U5.5

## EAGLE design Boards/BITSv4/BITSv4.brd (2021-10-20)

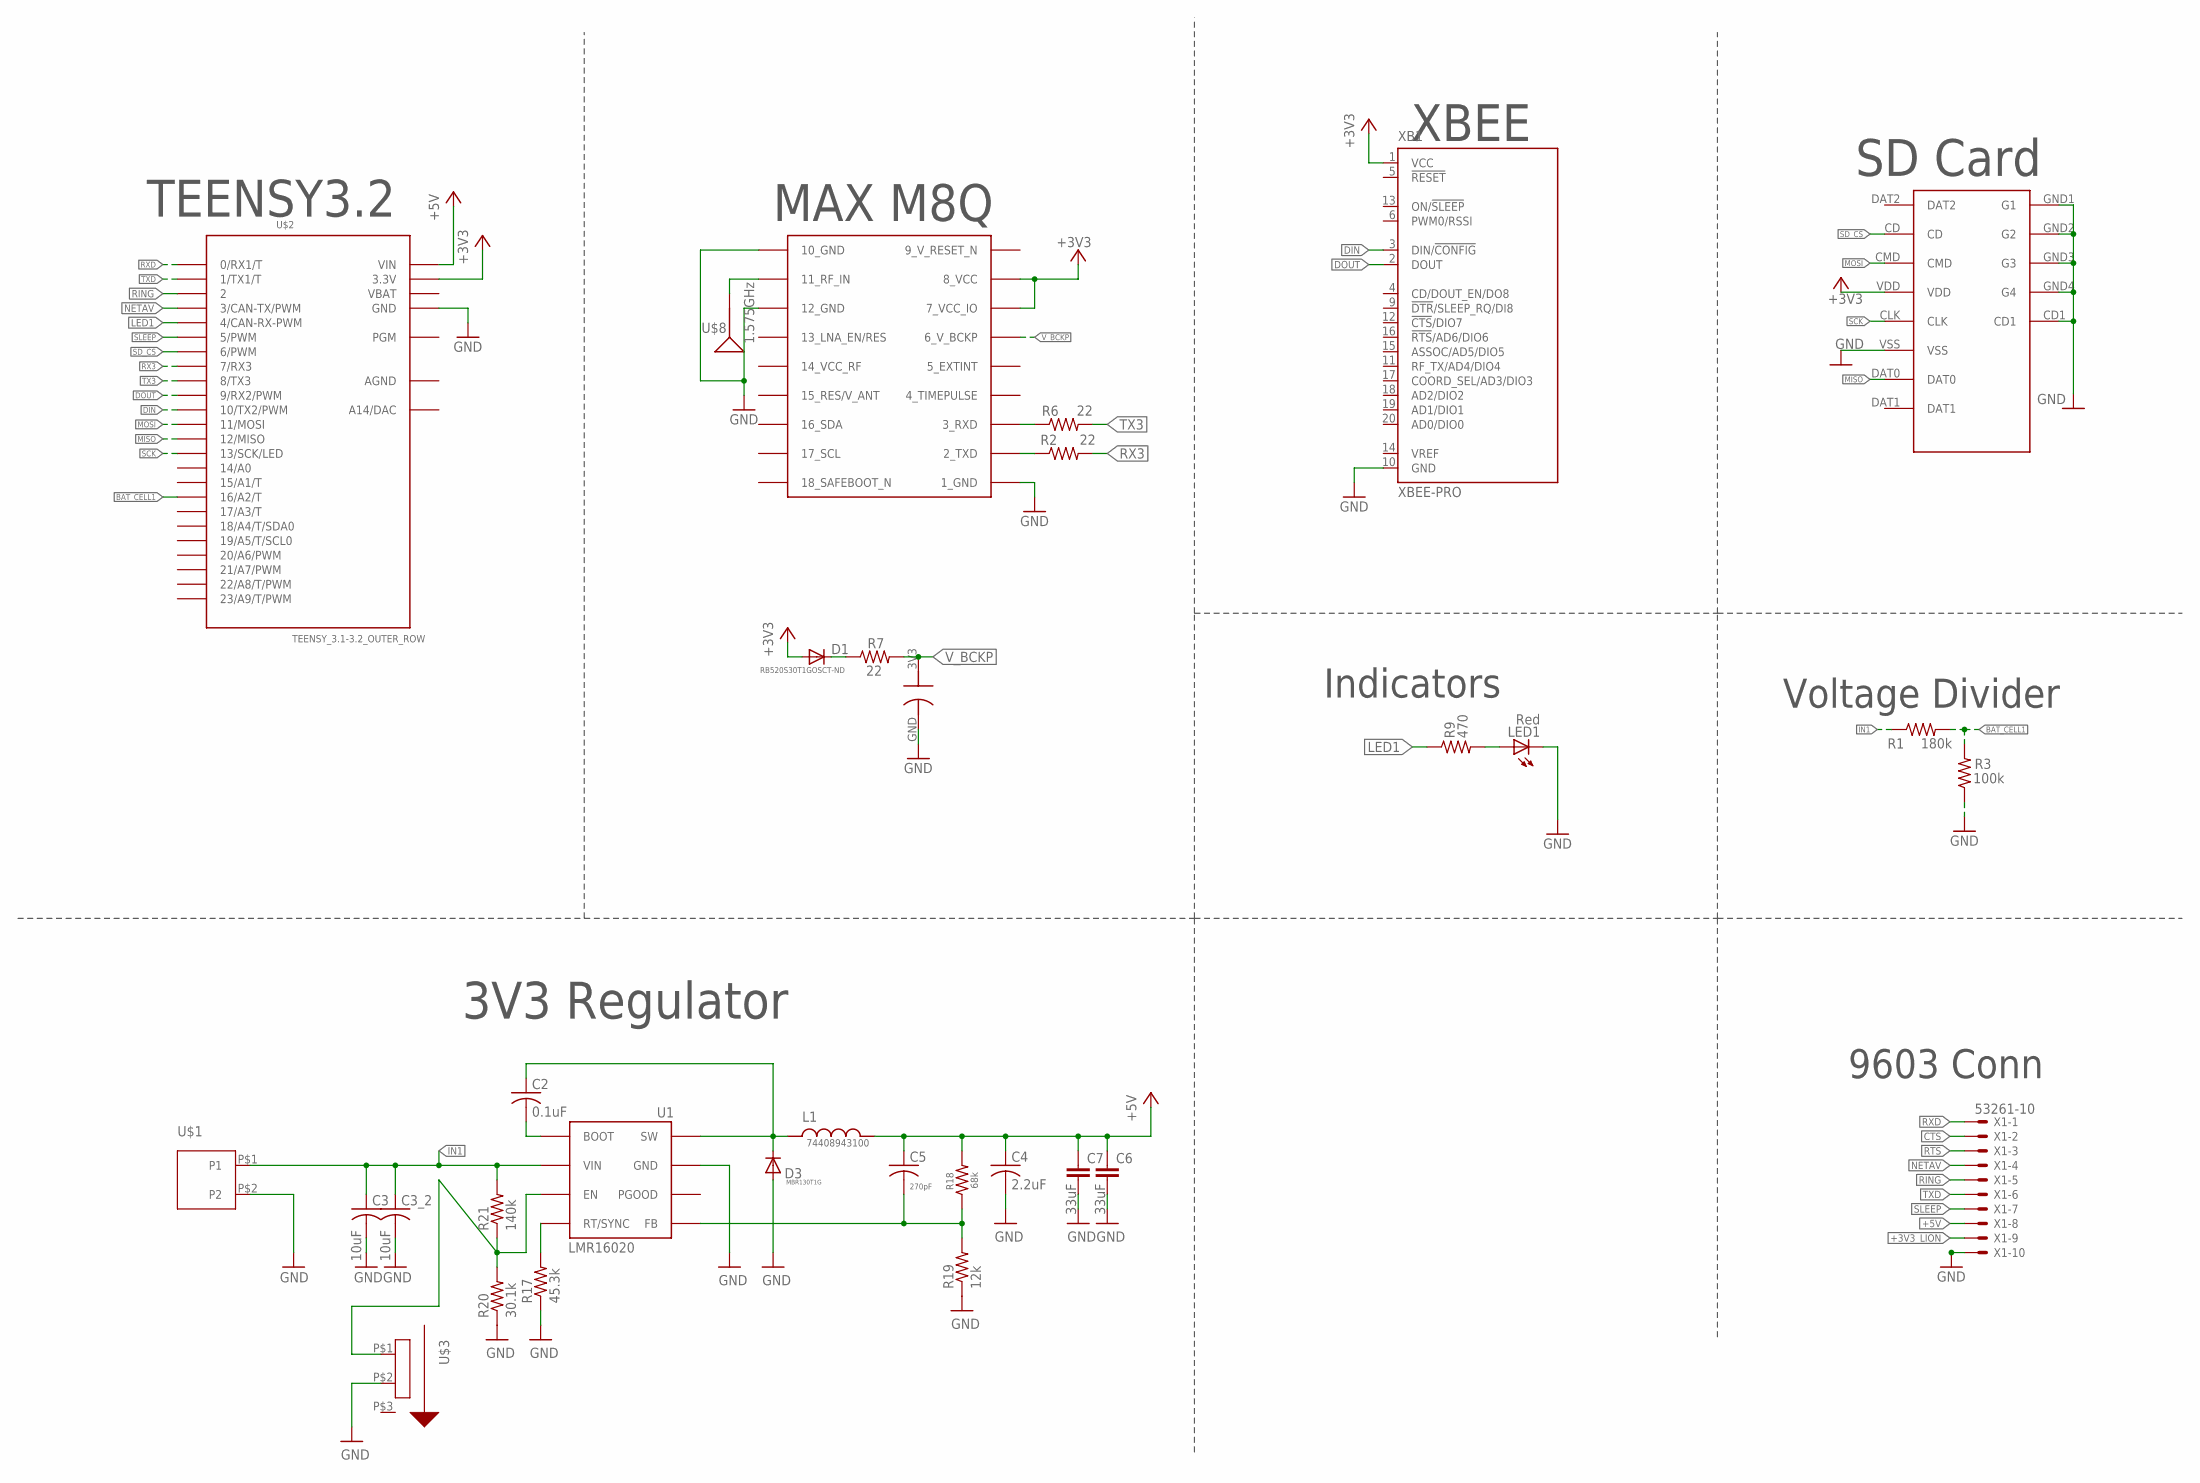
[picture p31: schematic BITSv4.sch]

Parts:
C1: 0.2F; ELNASUPERCAP
C2: 0.1uF; C0603
C3, C3_2: 10uF; C0805
C4: 2.2uF; C0603
C5: 270pF; C0402
C6, C7: 33uF; C050-024X044
D1: RB520S30T1GOSCT-ND; SOD523
D3: MBR130T1G; SOD-123_MINI-SMA
L1: 74408943100
LED1: Red; CHIP-LED0603
R1: 180k; R0603
R2, R6, R7: 22; R0603
R3: 100k; R0603
R9: 470; R0603
R17: 45.3k; R0603
R18: 68k; R0603
R19: 12k; R0603
R20: 30.1k; R0603
R21: 140k; R0603
U1: LMR16020; SO8
U$1: 559350210
U$2: TEENSY_3.1-3.2_OUTER_ROW; TEENSY_3.0-3.2&LC_OUTER_ROW
U$3: CL-SB-12B-01
U$4: MICRO_SD; MICRO_SD_HINGED
U$7: MAX-M8
U$8: 1.575GHz; SPARKFUN-GPS_ANT-GPS-2X7MM
X1: 53261-10
XB1: XBEE-PRO

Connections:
9_V_RESET_N: U$7.9_RESET_N (9_V_RESET_N)
+3V3: D1.A, U$2.3.3V, U$2.3.3V1 (3.3V), U$4.VDD, U$7.7_VCC_IO, U$7.8_VCC, XB1.1 (VCC)
+3V3_LION: X1.9
+5V: C4.1, C5.1, C6.1, C7.1, L1.P$2, R18.2, U$2.VIN, X1.8
AGND: U$2.AGND
BAT_CELL1: R1.2, R3.2, U$2.16/A2 (16/A2/T)
CTS: X1.2
DIN: U$2.10 (10/TX2/PWM), XB1.3 (DIN/!CONFIG)
DOUT: U$2.9 (9/RX2/PWM), XB1.2 (DOUT)
FB: C5.2, R18.1, R19.2, U1.P$5 (FB)
GND: C1.GND, C3.2, C3_2.2, C4.2, C6.2, C7.2, D3.A, LED1.C, R3.1, R17.1, R19.1, R20.1, U1.P$7 (GND), U1.PAD (GND), U$1.P$2 (P2), U$2.GND, U$2.GND1 (GND), U$3.P$2 (P2), U$4.CD1, U$4.GND1 (G1), U$4.GND2 (G2), U$4.GND3 (G3), U$4.GND4 (G4), U$4.VSS, U$7.1_GND, U$7.10_GND, U$7.12_GND, X1.10, XB1.10 (GND)
IN1: C3.1, C3_2.1, R1.1, R21.2, U1.P$2 (VIN), U$1.P$1 (P1)
LED1: R9.1, U$2.4 (4/CAN-RX-PWM)
MISO: U$2.12 (12/MISO), U$4.DAT0
MOSI: U$2.11 (11/MOSI), U$4.CMD
unnamed: U$7.11_RF_IN, U$8.1
unnamed: D1.C, R7.1
unnamed: R6.1, U$7.3_RXD
unnamed: R2.1, U$7.2_TXD
unnamed: LED1.A, R9.2
unnamed: R20.2, R21.1, U1.P$3 (EN), U$3.P$1 (P1)
unnamed: R17.2, U1.P$4 (RT/SYNC)
unnamed: C2.2, U1.P$1 (BOOT)
NETAV: U$2.3 (3/CAN-TX/PWM), X1.4
RING: U$2.2, X1.5
RTS: X1.3
RX3: R2.2, U$2.7 (7/RX3)
RXD: U$2.0 (0/RX1/T), X1.1
SCK: U$2.13 (13/SCK/LED), U$4.CLK
SD_CS: U$2.6 (6/PWM), U$4.CD
SLEEP: U$2.5 (5/PWM), X1.7
SW: C2.1, D3.C, L1.P$1, U1.P$8 (SW)
TX3: R6.2, U$2.8 (8/TX3)
TXD: U$2.1 (1/TX1/T), X1.6
VBAT: U$2.VBAT
V_BCKP: C1.3V3, R7.2, U$7.6_V_BCKP

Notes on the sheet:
MAX M8Q
TEENSY3.2
Voltage Divider
Indicators
SD Card
9603 Conn
3V3 Regulator
XBEE

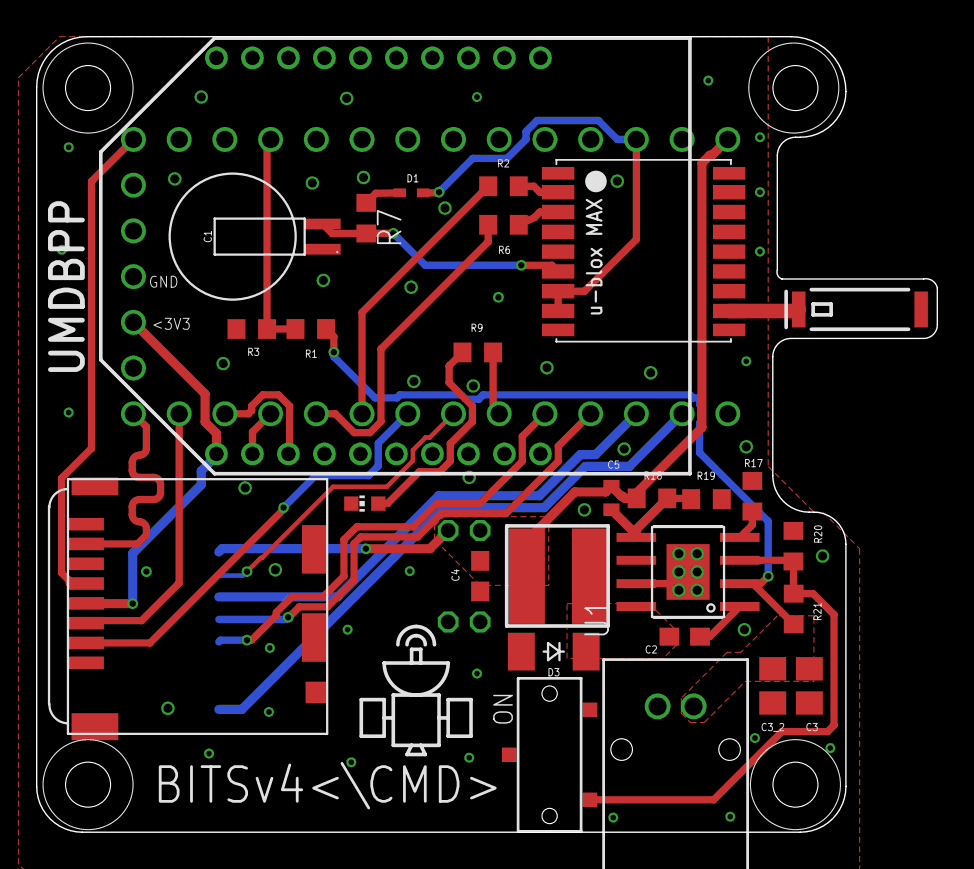
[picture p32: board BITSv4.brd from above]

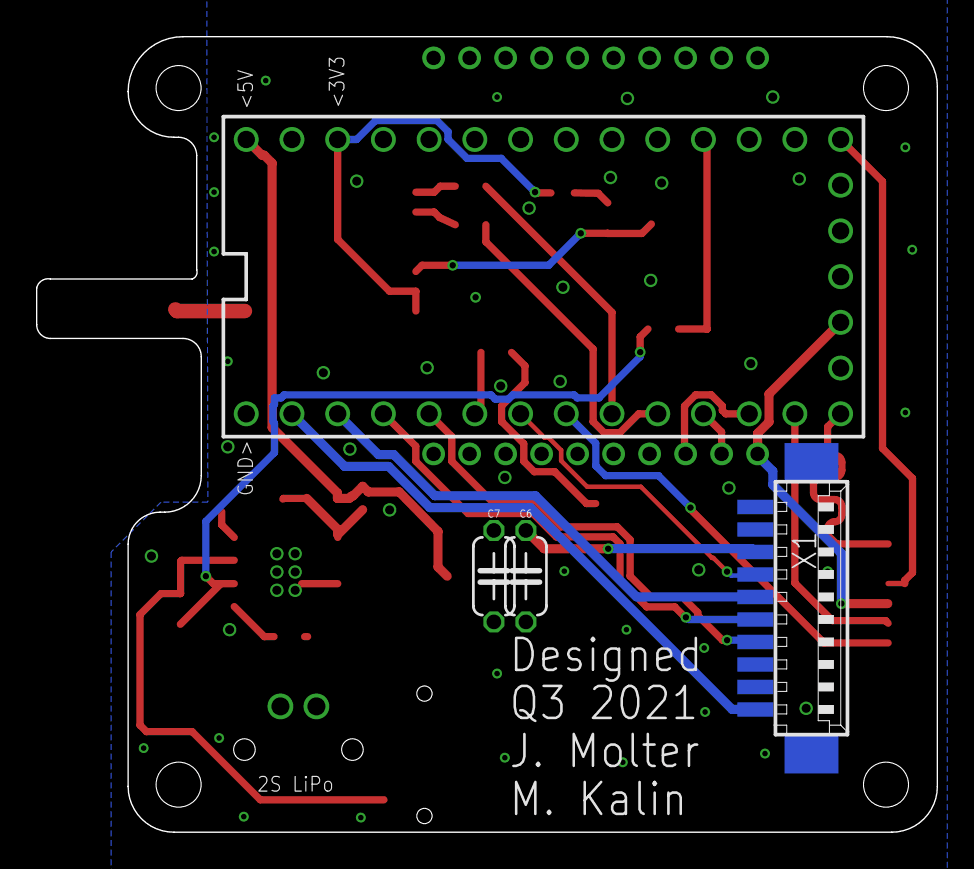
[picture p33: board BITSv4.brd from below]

Board: 2 copper layers, 50.0 x 44.2 mm, 32 parts (4 on the bottom side), 30 nets.

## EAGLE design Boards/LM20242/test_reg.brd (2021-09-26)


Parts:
C1, C2: 10u; C0805
C3, C5, C6: 10uF; C0805
C4: 6.8nF; C0805
C7: 47uF; C0805
R1: 95.3k; R0805
R2: 7.68k; R0805
R3: 60.4k; R0805
R4: 11.5k; R0805
U1: TI_NATIONAL_SEMICONDUCTOR_LM20242MHE-NOPBTI_NATIO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; TI_NATIONAL_SEMICONDUCTOR_LM20242MHE-NOPB_0

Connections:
GND: C1.2, C2.2, C3.2, C4.2, C6.2, C7.2, R1.1, R2.1, R4.1, U1.9 (3_GND), U1.10 (1_GND), U1.11 (2_GND), U1.12 (AGND), U1.21 (DAP)
unnamed: R1.2, U1.20 (RT)
unnamed: R2.2, U1.4 (COMP)
unnamed: C4.1, U1.1 (SS/TRK)
unnamed: C5.2, U1.7 (3_SW), U1.8 (4_SW), U1.13 (1_SW), U1.14 (2_SW)
unnamed: C5.1, U1.17 (BOOT)
unnamed: R3.1, R4.2, U1.2 (FB)
unnamed: C6.1, U1.18 (VCC)
VCC: C1.1, C2.1, C3.1, U1.5 (3_VIN), U1.6 (4_VIN), U1.15 (1_VIN), U1.16 (2_VIN)
VOUT: C7.1, R3.2


Board: 2 copper layers, 12 parts (0 on the bottom side), 10 nets.

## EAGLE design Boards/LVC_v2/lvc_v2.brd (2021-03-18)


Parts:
C2: 0.1uF; C0603
C3: 10 uF; C1210
C4: .18 uF; C0603
C5: 2.2 uF; C1210
C11: 10 uF; C0603
D3: DO-214AC
JP2: PINHD-1X7; 1X07
JP3: PINHD-1X1; 1X01
L1: ASPI-6045S-560M-TCT-ND; ABRACON
R17: 23.3k; R0603
R18: 340k; R0603
R19: 100k; R0603
R20: 30.1k; R0603
R21: 140k; R0603
U1: LMR16020; SO8
U$1: 559350210
U$3: CL-SB-12B-01

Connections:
+3V3: C4.1, C11.1, JP2.7, L1.P$2, R18.2
FB: R18.1, R19.2, U1.P$5 (FB)
GND: C3.2, C4.2, C5.2, C11.2, D3.P$1, JP3.1, R17.1, R19.1, R20.1, U1.P$7 (GND), U1.PAD (GND), U$1.P$2 (P2), U$3.P$2 (P2)
IN1: C3.1, C5.1, R21.2, U1.P$2 (VIN), U$1.P$1 (P1)
MISO_6: JP2.2
unnamed: R20.2, R21.1, U1.P$3 (EN), U$3.P$3 (P3)
unnamed: R17.2, U1.P$4 (RT/SYNC)
unnamed: C2.2, U1.P$1 (BOOT)
RST: JP2.6
SCK_7: JP2.3
SCL_16: JP2.5
SDA_17: JP2.4
STATUS: JP2.1
SW: C2.1, D3.P$2, L1.P$1, U1.P$8 (SW)

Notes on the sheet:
Connectors
NOTE: All resistors +/- 1.0% tolerance All capacitors +/- 10% tolerance
3V3 Regulator


Board: 2 copper layers, 24.8 x 23.0 mm, 17 parts (0 on the bottom side), 8 nets.

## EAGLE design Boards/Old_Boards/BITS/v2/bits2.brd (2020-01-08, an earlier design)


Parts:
C1: DCK-3R3E204T614-E; ELNASUPERCAP
D1: DIODE-SOD523; SOD523
LED1: Red; CHIP-LED0603
LED2: Green; CHIP-LED0603
R1, R4: 18k; R0603
R2, R6, R7: 22; R0603
R3, R5: 10k; R0603
R8: 100k; R0603
R9, R10: 470; R0603
R11: 100; R0603
T1: Si1013; SOT-23
U$1: MICROSD
U$2: TEENSY_3.1-3.2_ALL_PINS; TEENSY_3.0-3.2&LC_ALL_PINS
U$3: CR1220SMT; CR1220-SMD
U$7: MAX-M8
U$8: 1.575GHz; SPARKFUN-GPS_ANT-GPS-2X7MM
X1: 22-23-2021
X2: 53398-10
X3: 22-23-2031
X4: 22-23-2041

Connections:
9_V_RESET_N: U$7.9_RESET_N (9_V_RESET_N)
+3V3: D1.A, R8.1, T1.2 (S), U$1.4 (VDD), U$2.3.3V, U$2.3.3V1 (3.3V), X4.3
+5V: U$2.VIN, X1.2, X2.8
AGND: U$2.AGND
AREF: U$2.AREF
BAT_CELL1: R1.2, R3.2, U$2.14/A0
BAT_CELL2: R4.1, R5.1, U$2.15/A1 (15/A1/T)
CELL1: R1.1, X3.1
CELL2: R4.2, X3.2
CTS: X2.2
DIN: U$2.10 (10/TX2/PWM), X4.1
DOUT: U$2.9 (9/RX2/PWM), X4.2
GND: C1.GND, LED1.C, LED2.C, R3.1, R5.2, U$1.6 (VSS), U$1.MT1 (GND), U$1.MT2 (GND1), U$2.GND, U$2.GND1 (GND), U$3.-, U$7.1_GND, U$7.10_GND, U$7.12_GND, X1.1, X2.10, X3.3, X4.4
GPSON: R8.2, R11.2, U$2.6 (6/PWM)
LED1: R9.1, U$2.4 (4/CAN-RX/PWM)
LED2: R10.1, U$2.5 (5/PWM)
LIONIN: X2.9
MISO: U$1.7 (DATA_OUT), U$2.12 (12/MISO)
MOSI: U$1.3 (DATA_IN), U$2.11 (11/MOSI)
unnamed: U$7.11_RF_IN, U$8.1
unnamed: D1.C, R7.1
unnamed: R6.1, U$7.3_RXD
unnamed: R2.1, U$7.2_TXD
unnamed: LED2.A, R10.2
unnamed: LED1.A, R9.2
unnamed: R11.1, T1.3 (G)
unnamed: T1.1 (D), U$7.7_VCC_IO, U$7.8_VCC
NETAV: X2.4
RING: U$2.16/A2 (16/A2/T), X2.5
RTS: X2.3
RX3: R2.2, U$2.7 (7/RX3)
RXD: U$2.0 (0/RX1/T), X2.1
SCK: U$1.5 (SCLK), U$2.13 (13/SCK/LED)
SD_CS: U$1.2 (CS), U$2.3 (3/CAN-TX/PWM)
SLEEP: U$2.2, X2.7
TX3: R6.2, U$2.8 (8/TX3)
TXD: U$2.1 (1/TX1/T), X2.6
VBAT: U$2.VBAT, U$3.+$1 (+), U$3.+$2 (+1)
VUSB: U$2.VUSB
V_BCKP: C1.3V3, R7.2, U$7.6_V_BCKP

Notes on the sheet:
MAX M8Q
TEENSY3.2
RTC Battery
Cell Dividers
Indicators
Power
Headers
SD Card
Don't forget the oscillator
RockblockHeader
Battery Voltage
XBee



Board: 2 copper layers, 41.4 x 43.5 mm, 25 parts (2 on the bottom side), 32 nets.

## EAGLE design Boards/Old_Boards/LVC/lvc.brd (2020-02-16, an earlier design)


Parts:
C1: 0.33uF; C0603
C2, C4: 0.1uF; C0603
C3: 47pF; C0603
D1: BZT52B8V2; SOD123
D2, D3: DZ2J120M0L; SMINI2-F5-B
JP2: PINHD-1X7; 1X07
Q1: SI7997DP; POWERPAK-SO-8-DUAL
Q2: RK7002BMT116; SOT23
R1: R-US_R0603; R0603
R2, R4, R11: 100k; R0603
R3: 3k; R0603
R5, R6, R10: 1M; R0603
U1: NCP300LSN33T1G; SOT23-5
U2: L78L33ACUTR; SOT-89
U3: TLV170IDBVR; SOT23-DBV
U$1: MICROCLASP_4; 4_PIN_MICROCLASP
U$2, U$3: LITEAPRS

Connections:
EN: R5.1
GND: C1.2, C2.2, C3.2, C4.2, D1.A, Q2.2 (S), R4.2, R6.2, R10.2, R11.1, U1.3 (GND), U2.2 (GND), U3.2 (V-), U$1.P$3, U$1.P$4, U$2.P$2, U$3.P$2
LED: C2.1, U2.1 (VOUT)
LOAD: Q2.1 (G), R4.1, U1.1 (!RST!)
MISO_6: JP2.2
unnamed: R1.2, U$1.P$2
unnamed: D2.A, Q1.4 (G), R2.2, R3.1
unnamed: D3.A, Q1.2 (G), R10.1
unnamed: Q2.3 (D), R3.2
RST: JP2.6
SCK_7: JP2.3
SCL_16: JP2.5
SDA_17: JP2.4
STATUS: JP2.1, R1.1
V+: C4.1, D2.C, D3.C, Q1.1 (S), Q1.3 (S), R2.1, U3.5 (V+)
VDD: Q1.7 (D), Q1.8 (D), Q1.8L (D), U$1.P$1
VREG: C1.1, Q1.5 (D), Q1.5L (D), Q1.6 (D), U2.3 (VIN), U$2.P$1, U$3.P$1
V_DIV: D1.C, R5.2, R6.1, U3.3 (+IN)
V_DIV_BUF: C3.1, R11.2, U1.2 (VCC), U3.1 (OUT), U3.4 (-IN)

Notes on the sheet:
Voltage Regulator
Switching
Divider
Connectors
Reverse Polarity Protection
Cutoff
NOTE: All resistors +/- 1.0% tolerance All capacitors +/- 10% tolerance
C1 rated to at least 35 V
R3 rated to at least 0.2 W
Buffer


Board: 2 copper layers, 31.4 x 33.5 mm, 24 parts (0 on the bottom side), 13 nets.

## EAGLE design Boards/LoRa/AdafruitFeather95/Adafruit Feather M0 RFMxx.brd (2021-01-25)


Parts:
C1, C7, C14: 1uF; 0603-NO
C2, C4: 22pF; 0603-NO
C3, C6, C8: 10µF; 0805-NO
C5, C9: 10uF; 0805-NO
CHG: ORANGE; CHIPLED_0805_NOOUTLINE
D1: MBR120; SOD-123
JP1: HEADER-1X16ROUND; 1X16_ROUND
JP2: HEADER-1X1ROUND; 1X01_ROUND
JP3: HEADER-1X12; 1X12_ROUND
JP5: HEADER-1X3ROUND; 1X03_ROUND
L: RED; CHIPLED_0805_NOOUTLINE
R1, R3: 100k; 0603-NO
R2: 1K; 0603-NO
R6: 100K; 0603-NO
R7: 2.2K; 0603-NO
R8: 10K\; 0603-NO
SW1: SPST_TACT-KMR2; KMR2
TP1, TP2: TESTPOINTROUND1.5MM; TESTPOINT_ROUND_1.5MM
U2: AP2112K-3.3; SOT23-5
U3: MCP73831T-2ACI/OT; SOT23-5
U4: RFM69HCW; RFMHCW_SMT
U$4: ATSAMD21G18_QFN; TQFN48_7MM
U$31, U$32: MOUNTINGHOLE2.5; MOUNTINGHOLE_2.5_PLATED
U$34, U$35: FIDUCIAL""; FIDUCIAL_1MM
X1: JSTPH; JSTPH2
X2: 32.768; XTAL3215
X3: microUSB; 4UCONN_20329_V2
X4: uFL; U.FL

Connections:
!RESET: JP1.16, SW1.1, SW1.3 (P1), U$4.40 (/RESET)
+3V3: C5.1, C7.1, C8.1, C9.1, JP1.15, U2.5 (OUT), U4.5P (VDD), U$4.6 (VDDA), U$4.17 (VDDIO), U$4.36 (VDDIO), U$4.44 (VDDIN)
A0: JP1.12, U$4.3 (PA02/EINT2/AIN0/Y0/VOUT)
A1: JP1.11, U$4.7 (PB08/I8/AIN2/SERCOM4.0)
A2: JP1.10, U$4.8 (PB09/I9/AIN3/SERCOM4.1)
A3: JP1.9, U$4.9 (PA04/EINT4/VREFB/AIN4/SERCOM0.0)
A4: JP1.8, U$4.10 (PA05/EINT5/AIN5/SERCOM0.1)
A5: JP1.7, U$4.47 (PB02/I2/AIN10/SERCOM5.0)
ANT: JP2.1, U4.1P (ANT), X4.3 (SIGNAL)
AREF: C14.1, JP1.14, U$4.4 (PA03/EINT3/VREFA/AIN1)
D0: JP1.3, U$4.16 (PA11/I11/AIN19/SERCOM0+2.3/I2SF0)
D1: JP1.2, U$4.15 (PA10/I10/AIN18/SERCOM0+2.2/I2SCK)
D2: U$4.23 (PA14/I14/SERCOM2+4.2)
D3_IRQ: U4.6P (DIO0), U$4.14 (PA09/I2C/I9/AIN17/SERCOM0+2.1/I2SMC)
D4_RST: U4.14P (RESET), U$4.13 (PA08/I2C/AIN16/SERCOM0+2.0/I2SD1)
D5: JP3.10, U$4.24 (PA15/I15/SERCOM3+4.3)
D6: JP3.9, U$4.29 (PA20/I4/SERCOM3+5.2/I2SSC)
D7: U$4.30 (PA21/I5/SERCOM3+5.3/I2SFS0)
D8_CS: U4.13P (NSS), U$4.11 (PA06/EINT6/AIN6/SERCOM0.2)
D9: JP3.8, R3.2, R6.1, U$4.12 (PA07/I7/AIN7/SERCOM0.3/I2SD0)
D10: JP3.7, U$4.27 (PA18/I2/SERCOM1+3.2)
D11: JP3.6, U$4.25 (PA16/I2C/I0/SERCOM1+3.0)
D12: JP3.5, U$4.28 (PA19/I3/SERCOM1+3.3/I2SD0)
D13: JP3.4, R7.1, U$4.26 (PA17/I2C/I1/SERCOM1+3.1)
D+: U$4.34 (PA25/I13/SERCOM3+5.3/D+), X3.D+
D-: U$4.33 (PA24/I12/SERCOM3+5.2/D-), X3.D-
DIO1: JP1.1, U4.7P (DIO1)
DIO2: JP5.3, U4.8P (DIO2)
DIO3: JP5.2, U4.3P (DIO3)
DIO5: JP5.1, U4.15P (DIO5)
EN: JP3.2, R1.2, U2.3 (EN)
GND: C1.2, C2.2, C3.2, C4.2, C5.2, C6.2, C7.2, C8.2, C9.2, C14.2, JP1.13, L.C, R6.2, R8.2, SW1.2 (S), SW1.4 (S1), U2.2 (GND), U3.2 (VSS), U4.2P (GND), U4.9P (GND), U4.16P (GND), U$4.5 (GNDA), U$4.18 (GND), U$4.35 (GND), U$4.42 (GND), U$4.THERMAL (GND), X1.1, X3.BASE@1 (GND), X3.BASE@2 (GND), X3.GND, X3.SPRT@1 (GND), X3.SPRT@2 (GND), X3.SPRT@3 (GND), X3.SPRT@4 (GND), X4.1 (GND), X4.2 (GND)
MISO: JP1.4, U4.10P (MISO), U$4.21 (PA12/I12/I2C/SERCOM2+4.0)
MOSI: JP1.5, U4.11P (MOSI), U$4.19 (PB10/I10/SERCOM4.2/I2SMC)
unnamed: CHG.C, R2.1
unnamed: L.A, R7.2
unnamed: R2.2, U3.1 (STAT)
unnamed: R8.1, U3.5 (PROG)
unnamed: C2.1, U$4.1 (PA00/EINT0/SERCOM1.0), X2.P$1
unnamed: C4.1, U$4.2 (PA01/EINT1/SERCOM1.1), X2.P$2
SCK: JP1.6, U4.12P (SCK), U$4.20 (PB11/I11/SERCOM4.3/I2SCL)
SCL: JP3.11, U$4.32 (PA23/I2C/I7/SERCOM3+5.1/SOF)
SDA: JP3.12, U$4.31 (PA22/I2C/I6/SERCOM3+5.0)
SWCLK: TP1.P$1, U$4.45 (PA30/I10/SECOM1.2/SWCLK)
SWDIO: TP2.P$1, U$4.46 (PA31/I11/SECOM1.3/SWDIO)
VBAT: C3.1, D1.A, JP3.1, R3.1, U3.3 (VBAT), X1.2
VBUS: C6.1, CHG.A, D1.C, JP3.3, R1.1, U2.1 (IN), U3.4 (VDD), X3.VBUS
VDDCORE: C1.1, U$4.43 (VDDCORE)

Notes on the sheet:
POWER AND FILTERING
RESET
10K = 100mA
5.0K = 200mA
2.0K = 500mA
1.0K = 1000mA
N/C
TXLED
USBHOSTEN
RXLED
TXD
RXD
USB AND BATTERY CHARGING
BREAKOUTS
RED LED

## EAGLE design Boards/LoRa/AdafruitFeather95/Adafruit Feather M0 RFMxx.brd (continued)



Board: 2 copper layers, 50.8 x 22.9 mm, 42 parts (6 on the bottom side), 46 nets.

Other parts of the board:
U$7, U$12: ADAFRUIT_3.5MM
U$9: FEATHERLOGO
U$13: PCBFEAT-REV-040

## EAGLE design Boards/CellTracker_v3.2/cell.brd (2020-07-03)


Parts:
C1: DCK-3R3E204T614-E; ELNASUPERCAP
C6: 0.1 uF; C0805
C7: .18uF; C0603
C8: 10 uF; C0603
C9: 10 uF; C1210
C10: 2.2 uF; C1210
D1: RB520S30T1G; SOD523
D2: DO-214AC
L1: ASPI-6045S-560M-TCT-ND; ABRACON
LED1: Green; CHIP-LED0603
R1, R8: 470; R0603
R2, R6, R7: 22; R0603
R3: 23.3k; R0603
R4: 340k; R0603
R5: 100k; R0603
R9: 30.1k; R0603
R10: 140k; R0603
U2: LMR16020; SO8
U$1: TEENSY_3.1-3.2_OUTER_ROW; TEENSY_3.0-3.2&LC_OUTER_ROW
U$3: MICRO_SD; MICRO_SD_HINGED
U$4: MICROCLASP_4; 4_PIN_MICROCLASP
U$7: MAX-M8
U$8: 1.575GHz; SPARKFUN-GPS_ANT-GPS-2X7MM
XB1: XBEE-LTE-M; XBEE-PRO

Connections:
9_V_RESET_N: U$7.9_RESET_N (9_V_RESET_N)
+3V3: C7.1, C8.1, D1.A, L1.P$2, R4.2, U$1.3.3V, U$1.3.3V1 (3.3V), U$3.VDD, U$7.7_VCC_IO, U$7.8_VCC, XB1.1 (VCC); also elsewhere on the board
AGND: U$1.AGND
EN: R9.2, R10.1, U2.P$3 (EN)
FB: R4.1, R5.2, U2.P$5 (FB)
GND: C1.GND, C7.2, C8.2, C9.2, C10.2, D2.P$1, LED1.C, R3.1, R5.1, R9.1, U2.P$7 (GND), U2.PAD (GND), U$1.GND, U$1.GND1 (GND), U$3.CD1, U$3.GND1 (G1), U$3.GND2 (G2), U$3.GND3 (G3), U$3.GND4 (G4), U$3.VSS, U$4.P$3, U$4.P$4, U$7.1_GND, U$7.10_GND, U$7.12_GND, XB1.10 (GND); also elsewhere on the board
MISO: U$1.12 (12/MISO), U$3.DAT0
MOSI: U$1.11 (11/MOSI), U$3.CMD
unnamed: U$7.11_RF_IN, U$8.1
unnamed: R1.2, U$1.14/A0
unnamed: R6.1, U$7.3_RXD
unnamed: R2.1, U$7.2_TXD
unnamed: C1.3V3, R7.1, U$7.6_V_BCKP
unnamed: R3.2, U2.P$4 (RT/SYNC)
unnamed: C6.2, U2.P$1 (BOOT)
unnamed: LED1.A, R1.1
unnamed: D1.C, R7.2
unnamed: R8.2, U$4.P$1
RX1: U$1.0 (0/RX1/T), XB1.2 (DOUT)
RX3: R2.2, U$1.7 (7/RX3)
SCK: U$1.13 (13/SCK/LED), U$3.CLK
SD_CS: U$1.10 (10/TX2/PWM), U$3.CD
SW: C6.1, D2.P$2, L1.P$1, U2.P$8 (SW)
SWITCH_LED: R8.1, U$1.3 (3/CAN-TX/PWM)
TX1: U$1.1 (1/TX1/T), XB1.3 (DIN/!CONFIG)
TX3: R6.2, U$1.8 (8/TX3)
VBAT: U$1.VBAT

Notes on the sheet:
MAX M8Q
SD Card
XBee
Teensy3.2
3V3 Regulator

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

Board: 2 copper layers, 44.7 x 41.9 mm, 30 parts (1 on the bottom side), 27 nets.

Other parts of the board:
C2, C3: 0.1uF; C0603
ISO7021: ISO7021; 8-SOIC

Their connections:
+3V3: C2.1, ISO7021.P$1; also elsewhere on the board
GND: C2.2, ISO7021.P$4; also elsewhere on the board
GND_EX: C3.2, ISO7021.P$5
VCC_EX: C3.1, ISO7021.P$8

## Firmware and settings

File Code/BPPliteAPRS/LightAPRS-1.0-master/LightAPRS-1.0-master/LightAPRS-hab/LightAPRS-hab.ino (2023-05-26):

#include <LibAPRS.h>        //Modified version of https://github.com/markqvist/LibAPRS
#include <SoftwareSerial.h>
#include <TinyGPS++.h>      //https://github.com/mikalhart/TinyGPSPlus
#include <LowPower.h>       //https://github.com/rocketscream/Low-Power
#include <Wire.h>
#include <Adafruit_BMP085.h>//https://github.com/adafruit/Adafruit-BMP085-Library
#include <avr/wdt.h>

#define RfPDPin     19
#define GpsVccPin   18
#define RfPwrHLPin  21
#define RfPttPin    20
#define BattPin     A2
#define PIN_DRA_RX  22
#define PIN_DRA_TX  23

#define ADC_REFERENCE REF_3V3
#define OPEN_SQUELCH false

#define GpsON         digitalWrite(GpsVccPin, LOW)//PNP
#define GpsOFF        digitalWrite(GpsVccPin, HIGH)
#define RfON          digitalWrite(RfPDPin, HIGH)
#define RfOFF         digitalWrite(RfPDPin, LOW)
#define RfPwrHigh     pinMode(RfPwrHLPin, INPUT)
#define RfPwrLow      pinMode(RfPwrHLPin, OUTPUT);digitalWrite(RfPwrHLPin, LOW)
#define RfPttON       digitalWrite(RfPttPin, HIGH)//NPN
#define RfPttOFF      digitalWrite(RfPttPin, LOW)
#define AprsPinInput  pinMode(12,INPUT);pinMode(13,INPUT);pinMode(14,INPUT);pinMode(15,INPUT)
#define AprsPinOutput pinMode(12,OUTPUT);pinMode(13,OUTPUT);pinMode(14,OUTPUT);pinMode(15,OUTPUT)

#define DEVMODE // Development mode. Uncomment to enable for debugging.

//****************************************************************************
char  CallSign[7]="KC3SKW"; //DO NOT FORGET TO CHANGE YOUR CALLSIGN

int   CallNumber=8; //SSID http://www.aprs.org/aprs11/SSIDs.txt

char  Symbol='O'; // '/O' for balloon, '/>' for car, for more info : http://www.aprs.org/symbols/symbols-new.txt
bool alternateSymbolTable = false ; //false = '/' , true = '\'

char Frequency[9]="144.3900"; //default frequency. 144.3900 for US, 144.8000 for Europe

char comment[50] = "umdbpp"; // Max 50 char
char StatusMessage[50] = "umdbpp"; 

double prev_alt = 0.0;
int prev_time = 0.0;

//*****************************************************************************
unsigned int   BeaconWait=64;  //seconds sleep for next beacon (TX).
unsigned int   BattWait=60;    //seconds sleep if super capacitors/batteries are below BattMin (important if power source is solar panel) 
float BattMin=4.5;        // min Volts to wake up.
float DraHighVolt=1.0;    // min Volts for radio module (DRA818V) to transmit (TX) 1 Watt, below this transmit 0.5 Watt. You don't need 1 watt on a balloon. Do not change this.
//float GpsMinVolt=4.0; //min Volts for GPS to wake up. (important if power source is solar panel) 

boolean aliveStatus = true; //for tx status message on first wake-up just once.

//do not change WIDE path settings below if you don't know what you are doing :) 
byte  Wide1=0; // 1 for WIDE1-1 path
byte  Wide2=0; // 1 for WIDE2-1 path

/**
Airborne stations above a few thousand feet should ideally use NO path at all, or at the maximum just WIDE2-1 alone.  
Due to their extended transmit range due to elevation, multiple digipeater hops are not required by airborne stations.  
Multi-hop paths just add needless congestion on the shared APRS channel in areas hundreds of miles away from the aircraft's own location.  
NEVER use WIDE1-1 in an airborne path, since this can potentially trigger hundreds of home stations simultaneously over a radius of 150-200 miles. 
 */
int pathSize=0; // 2 for WIDE1-N,WIDE2-N ; 1 for WIDE2-N
boolean autoPathSizeHighAlt = true; //force path to WIDE2-N only for high altitude (airborne) beaconing (over 1.000 meters (3.280 feet)) 

//boolean GpsFirstFix=false;
boolean ublox_high_alt_mode = false;

static char telemetry_buff[100];// telemetry buffer
uint16_t TxCount = 1;

TinyGPSPlus gps;
Adafruit_BMP085 bmp;
String serialCommand;


void setup() {
  wdt_enable(WDTO_8S);
  analogReference(INTERNAL2V56);
  pinMode(RfPDPin, OUTPUT);
  pinMode(GpsVccPin, OUTPUT);
  pinMode(RfPwrHLPin, OUTPUT);
  pinMode(RfPttPin, OUTPUT);
  pinMode(BattPin, INPUT);
  pinMode(PIN_DRA_TX,INPUT);

  RfOFF;

  //GpsOFF;

  GpsON;
  RfPwrLow;
  RfPttOFF;
  AprsPinInput;

  Serial.begin(57600);
  Serial1.begin(9600);
  
#if defined(DEVMODE)
  Serial.println(F("Start"));
#endif
  Serial.println("INIT");
      
  APRS_init(ADC_REFERENCE, OPEN_SQUELCH);
  APRS_setCallsign(CallSign,CallNumber);
  APRS_setDestination("APLIGA", 0);
  APRS_setMessageDestination("APLIGA", 0);
  APRS_setPath1("WIDE1", Wide1);
  APRS_setPath2("WIDE2", Wide2);
  APRS_useAlternateSymbolTable(alternateSymbolTable); 
  APRS_setSymbol(Symbol);
  //increase following value (for example to 500UL) if you experience packet loss/decode issues. 
  APRS_setPreamble(350UL);  
  APRS_setPathSize(pathSize);

  configDra818(Frequency);

  bmp.begin();
 
}

void loop() {
   wdt_reset();
  
  if (1==1) {
  
  if(aliveStatus){

      //send status tx on startup once (before gps fix)
      
      #if defined(DEVMODE)
        Serial.println(F("Sending"));
      #endif
      sendStatus();
      #if defined(DEVMODE)
        Serial.println(F("Sent"));
      #endif
      
      aliveStatus = false;
      
   }
    
    updateGpsData(1000);
    gpsDebug();

    
    if ((gps.location.age() < 1000 || gps.location.isUpdated()) && gps.location.isValid()) {
      if (gps.satellites.isValid() && (gps.satellites.value() > 3)) {
      updatePosition();
      updateTelemetry();
      
      //GpsOFF;
      setGPS_PowerSaveMode();
      //GpsFirstFix=true;

      if(autoPathSizeHighAlt && gps.altitude.feet()>3000){
            //force to use high altitude settings (WIDE2-n)
            APRS_setPathSize(1);
        } else {
            //use defualt settings  
            APRS_setPathSize(pathSize);
        }
      
      //send status message every 60 minutes
      if(gps.time.minute() == 30){               
        sendStatus();       
      } else {

         sendLocation();

      }

      freeMem();
      Serial.flush();
      sleepSeconds(BeaconWait);

      } else {
#if defined(DEVMODE)
      Serial.println(F("Not enough sattelites"));
#endif
      }
    } 
  } else {

    sleepSeconds(BattWait);
    
  }
  
}

void aprs_msg_callback(struct AX25Msg *msg) {
  //do not remove this function, necessary for LibAPRS
}

void sleepSeconds(int sec) {  
  //if(GpsFirstFix)GpsOFF;//sleep gps after first fix
  RfOFF;
  RfPttOFF;
  Serial.flush();
  wdt_disable();
  for (int i = 0; i < sec; i++) {
    //if(readBatt() < GpsMinVolt) GpsOFF;  //(for pico balloon only)
    LowPower.powerDown(SLEEP_1S, ADC_OFF, BOD_ON);   
  }
   wdt_enable(WDTO_8S);
}



byte configDra818(char *freq)
{
  SoftwareSerial Serial_dra(PIN_DRA_RX, PIN_DRA_TX);
  Serial_dra.begin(9600);
  RfON;
  char ack[3];
  int n;
  delay(2000);
  char cmd[50];
  sprintf(cmd, "AT+DMOSETGROUP=0,%s,%s,0000,4,0000", freq, freq);
  Serial_dra.println(cmd);
  ack[2] = 0;
  while (ack[2] != 0xa)
  {
    if (Serial_dra.available() > 0) {
      ack[0] = ack[1];
      ack[1] = ack[2];
      ack[2] = Serial_dra.read();
    }
  }
  Serial_dra.end();
  RfOFF;
  pinMode(PIN_DRA_TX,INPUT);
#if defined(DEVMODE)
  if (ack[0] == 0x30) Serial.println(F("Frequency updated...")); else Serial.println(F("Frequency update error!"));
#endif
  return (ack[0] == 0x30) ? 1 : 0;
}

void updatePosition() {
  // Convert and set latitude NMEA string Degree Minute Hundreths of minutes ddmm.hh[S,N].
  char latStr[10];
  int temp = 0;

  double d_lat = gps.location.lat();
  double dm_lat = 0.0;

  if (d_lat < 0.0) {
    temp = -(int)d_lat;
    dm_lat = temp * 100.0 - (d_lat + temp) * 60.0;
  } else {
    temp = (int)d_lat;
    dm_lat = temp * 100 + (d_lat - temp) * 60.0;
  }

  dtostrf(dm_lat, 7, 2, latStr);

  if (dm_lat < 1000) {
    latStr[0] = '0';
  }

  if (d_lat >= 0.0) {
    latStr[7] = 'N';
  } else {
    latStr[7] = 'S';
  }

  APRS_setLat(latStr);

  // Convert and set longitude NMEA string Degree Minute Hundreths of minutes ddmm.hh[E,W].
  char lonStr[10];
  double d_lon = gps.location.lng();
  double dm_lon = 0.0;

  if (d_lon < 0.0) {
    temp = -(int)d_lon;
    dm_lon = temp * 100.0 - (d_lon + temp) * 60.0;
  } else {
    temp = (int)d_lon;
    dm_lon = temp * 100 + (d_lon - temp) * 60.0;
  }

  dtostrf(dm_lon, 8, 2, lonStr);

  if (dm_lon < 10000) {
    lonStr[0] = '0';
  }
  if (dm_lon < 1000) {
    lonStr[1] = '0';
  }

  if (d_lon >= 0.0) {
    lonStr[8] = 'E';
  } else {
    lonStr[8] = 'W';
  }

  APRS_setLon(lonStr);
}

void updateTelemetry() { 
  sprintf(telemetry_buff, "%03d", gps.course.isValid() ? (int)gps.course.deg() : 0);
  telemetry_buff[3] += '/';
  sprintf(telemetry_buff + 4, "%03d", gps.speed.isValid() ? (int)gps.speed.knots() : 0);
  telemetry_buff[7] = '/';
  telemetry_buff[8] = 'A';
  telemetry_buff[9] = '=';
  sprintf(telemetry_buff + 10, "%06lu", (long)gps.altitude.feet());
  telemetry_buff[16] = ' ';
  sprintf(telemetry_buff + 17, "%03d", TxCount);
  telemetry_buff[20] = 'T';
  telemetry_buff[21] = 'x';
  telemetry_buff[22] = 'C';
  telemetry_buff[23] = ' '; float tempC = bmp.readTemperature();//-21.4;//
  dtostrf(tempC, 6, 2, telemetry_buff + 24);
  telemetry_buff[30] = 'C';
  telemetry_buff[31] = ' '; float pressure = bmp.readPressure() / 100.0; //Pa to hPa
  dtostrf(pressure, 7, 2, telemetry_buff + 32);
  telemetry_buff[39] = 'h';
  telemetry_buff[40] = 'P';
  telemetry_buff[41] = 'a';
  telemetry_buff[42] = ' ';
  dtostrf(readBatt(), 5, 2, telemetry_buff + 43);
  telemetry_buff[48] = 'V';
  telemetry_buff[49] = ' ';
  sprintf(telemetry_buff + 50, "%02d", gps.satellites.isValid() ? (int)gps.satellites.value() : 0);
  telemetry_buff[52] = 'S';
  telemetry_buff[53] = ' ';
  double alt = gps.altitude.meters();
  double curr_time = gps.time.hour()*3600 + gps.time.minute()*60 + gps.time.second();
  double ascent_rate = (alt - prev_alt)/(curr_time - prev_time);
  prev_alt = alt;
  prev_time = curr_time;
  dtostrf(ascent_rate, 4, 1, telemetry_buff + 54);
  telemetry_buff[58] = 'm';
  telemetry_buff[59] = '/';
  telemetry_buff[60] = 's';
  telemetry_buff[61] = 'V';
  telemetry_buff[62] = ' ';
  sprintf(telemetry_buff + 63, "%s", comment);

#if defined(DEVMODE)
  Serial.println(telemetry_buff);
#endif

}


void sendLocation() {

#if defined(DEVMODE)
      Serial.println(F("Location sending with comment"));
#endif
  if ((readBatt() > DraHighVolt) && (readBatt() < 10)) RfPwrHigh; //DRA Power 1 Watt
  else RfPwrLow; //DRA Power 0.5 Watt

  int hh = gps.time.hour();
  int mm = gps.time.minute();
  int ss = gps.time.second();

  char timestamp_buff[7];

  sprintf(timestamp_buff, "%02d", gps.time.isValid() ? (int)gps.time.hour() : 0);
  sprintf(timestamp_buff + 2, "%02d", gps.time.isValid() ? (int)gps.time.minute() : 0);
  sprintf(timestamp_buff + 4, "%02d", gps.time.isValid() ? (int)gps.time.second() : 0);
  timestamp_buff[6] = 'h';

  RfON;
  delay(2000);
  RfPttON;
  delay(1000);
  
  //APRS_sendLoc(telemetry_buff, strlen(telemetry_buff)); //beacon without timestamp
  APRS_sendLocWtTmStmp(telemetry_buff, strlen(telemetry_buff), timestamp_buff); //beacon with timestamp
  
  while(digitalRead(1)){;}//LibAprs TX Led pin PB1
  delay(50);
  RfPttOFF;
  RfOFF;
#if defined(DEVMODE)
  Serial.println(F("Location sent with comment"));
#endif

  TxCount++;
}

void sendStatus() {
  if ((readBatt() > DraHighVolt) && (readBatt() < 10)) RfPwrHigh; //DRA Power 1 Watt
  else RfPwrLow; //DRA Power 0.5 Watt

  RfON;
  delay(2000);
  RfPttON;
  delay(1000);
    
  APRS_sendStatus(StatusMessage, strlen(StatusMessage));

  while(digitalRead(1)){;}//LibAprs TX Led pin PB1
  delay(50);
  RfPttOFF;
  RfOFF;
#if defined(DEVMODE)
  Serial.println(F("Status sent"));
#endif

  TxCount++;

}


static void updateGpsData(int ms)
{
  GpsON;

  //if(!ublox_high_alt_mode){
      //enable ublox high altitude mode
      delay(100);
      setGPS_DynamicModel6();
      ublox_high_alt_mode = true;
   //}

  while (!Serial1) {
    delayMicroseconds(1); // wait for serial port to connect.
  }
    unsigned long start = millis();
    unsigned long bekle=0;
    do
    {
      while (Serial1.available()>0) {
        char c;
        c=Serial1.read();
        gps.encode(c);
        bekle= millis();
      }
      if (bekle!=0 && bekle+10<millis())break;
    } while (millis() - start < ms);

}

float readBatt() {
  float R1 = 560000.0; // 560K
  float R2 = 100000.0; // 100K
  float value = 0.0;
  do { 
    value =analogRead(BattPin);
    delay(5);
    value =analogRead(BattPin);
    value=value-8;
    value = (value * 2.56) / 1024.0;
    value = value / (R2/(R1+R2));
  } while (value > 16.0);
  return value ;
}

void freeMem() {
#if defined(DEVMODE)
  Serial.print(F("Free RAM: ")); Serial.print(freeMemory()); Serial.println(F(" byte"));
#endif
}

void gpsDebug() {
#if defined(DEVMODE)
  Serial.println();
  Serial.println(F("Sats HDOP Latitude   Longitude   Fix  Date       Time     Date Alt    Course Speed Card Chars Sentences Checksum"));
  Serial.println(F("          (deg)      (deg)       Age                      Age  (m)    --- from GPS ----  RX    RX        Fail"));
  Serial.println(F("-----------------------------------------------------------------------------------------------------------------"));

  printInt(gps.satellites.value(), gps.satellites.isValid(), 5);
  printInt(gps.hdop.value(), gps.hdop.isValid(), 5);
  printFloat(gps.location.lat(), gps.location.isValid(), 11, 6);
  printFloat(gps.location.lng(), gps.location.isValid(), 12, 6);
  printInt(gps.location.age(), gps.location.isValid(), 5);
  printDateTime(gps.date, gps.time);
  printFloat(gps.altitude.meters(), gps.altitude.isValid(), 7, 2);
  printFloat(gps.course.deg(), gps.course.isValid(), 7, 2);
  printFloat(gps.speed.kmph(), gps.speed.isValid(), 6, 2);
  printStr(gps.course.isValid() ? TinyGPSPlus::cardinal(gps.course.value()) : "*** ", 6);

  printInt(gps.charsProcessed(), true, 6);
  printInt(gps.sentencesWithFix(), true, 10);
  printInt(gps.failedChecksum(), true, 9);
  Serial.println();

#endif
}


static void printFloat(float val, bool valid, int len, int prec)
{
#if defined(DEVMODE)
  if (!valid)
  {
    while (len-- > 1)
      Serial.print('*');
    Serial.print(' ');
  }
  else
  {
    Serial.print(val, prec);
    int vi = abs((int)val);
    int flen = prec + (val < 0.0 ? 2 : 1); // . and -
    flen += vi >= 1000 ? 4 : vi >= 100 ? 3 : vi >= 10 ? 2 : 1;
    for (int i = flen; i < len; ++i)
      Serial.print(' ');
  }
#endif
}

static void printInt(unsigned long val, bool valid, int len)
{
#if defined(DEVMODE)
  char sz[32] = "*****************";
  if (valid)
    sprintf(sz, "%ld", val);
  sz[len] = 0;
  for (int i = strlen(sz); i < len; ++i)
    sz[i] = ' ';
  if (len > 0)
    sz[len - 1] = ' ';
  Serial.print(sz);
#endif
}

static void printDateTime(TinyGPSDate &d, TinyGPSTime &t)
{
#if defined(DEVMODE)
  if (!d.isValid())
  {
    Serial.print(F("********** "));
  }
  else
  {
    char sz[32];
    sprintf(sz, "%02d/%02d/%02d ", d.month(), d.day(), d.year());
    Serial.print(sz);
  }

  if (!t.isValid())
  {
    Serial.print(F("******** "));
  }
  else
  {
    char sz[32];
    sprintf(sz, "%02d:%02d:%02d ", t.hour(), t.minute(), t.second());
    Serial.print(sz);
  }

  printInt(d.age(), d.isValid(), 5);
#endif
}

static void printStr(const char *str, int len)
{
#if defined(DEVMODE)
  int slen = strlen(str);
  for (int i = 0; i < len; ++i)
    Serial.print(i < slen ? str[i] : ' ');
#endif
}
//following GPS code from : https://github.com/HABduino/HABduino/blob/master/Software/habduino_v4/habduino_v4.ino
void setGPS_DynamicModel6()
{
 int gps_set_sucess=0;
 uint8_t setdm6[] = {
 0xB5, 0x62, 0x06, 0x24, 0x24, 0x00, 0xFF, 0xFF, 0x06,
 0x03, 0x00, 0x00, 0x00, 0x00, 0x10, 0x27, 0x00, 0x00,
 0x05, 0x00, 0xFA, 0x00, 0xFA, 0x00, 0x64, 0x00, 0x2C,
 0x01, 0x00, 0x00, 0x00, 0x00, 0x00, 0x00, 0x00, 0x00,
 0x00, 0x00, 0x00, 0x00, 0x00, 0x00, 0x16, 0xDC };
 
 while(!gps_set_sucess)
 {
 sendUBX(setdm6, sizeof(setdm6)/sizeof(uint8_t));
 gps_set_sucess=getUBX_ACK(setdm6);
 }
}

void setGPS_DynamicModel3()
{
  int gps_set_sucess=0;
  uint8_t setdm3[] = {
    0xB5, 0x62, 0x06, 0x24, 0x24, 0x00, 0xFF, 0xFF, 0x03,
    0x03, 0x00, 0x00, 0x00, 0x00, 0x10, 0x27, 0x00, 0x00,
    0x05, 0x00, 0xFA, 0x00, 0xFA, 0x00, 0x64, 0x00, 0x2C,
    0x01, 0x00, 0x00, 0x00, 0x00, 0x00, 0x00, 0x00, 0x00,
    0x00, 0x00, 0x00, 0x00, 0x00, 0x00, 0x13, 0x76           };
  while(!gps_set_sucess)
  {
    sendUBX(setdm3, sizeof(setdm3)/sizeof(uint8_t));
    gps_set_sucess=getUBX_ACK(setdm3);
  }
}

void sendUBX(uint8_t *MSG, uint8_t len) {
 Serial1.flush();
 Serial1.write(0xFF);
 _delay_ms(500);
 for(int i=0; i<len; i++) {
 Serial1.write(MSG[i]);
 }
}
boolean getUBX_ACK(uint8_t *MSG) {
 uint8_t b;
 uint8_t ackByteID = 0;
 uint8_t ackPacket[10];
 unsigned long startTime = millis();
 
// Construct the expected ACK packet
 ackPacket[0] = 0xB5; // header
 ackPacket[1] = 0x62; // header
 ackPacket[2] = 0x05; // class
 ackPacket[3] = 0x01; // id
 ackPacket[4] = 0x02; // length
 ackPacket[5] = 0x00;
 ackPacket[6] = MSG[2]; // ACK class
 ackPacket[7] = MSG[3]; // ACK id
 ackPacket[8] = 0; // CK_A
 ackPacket[9] = 0; // CK_B
 
// Calculate the checksums
 for (uint8_t ubxi=2; ubxi<8; ubxi++) {
 ackPacket[8] = ackPacket[8] + ackPacket[ubxi];
 ackPacket[9] = ackPacket[9] + ackPacket[8];
 }
 
while (1) {
 
// Test for success
 if (ackByteID > 9) {
 // All packets in order!
 return true;
 }
 
// Timeout if no valid response in 3 seconds
 if (millis() - startTime > 3000) {
 return false;
 }
 
// Make sure data is available to read
 if (Serial1.available()) {
 b = Serial1.read();
 
// Check that bytes arrive in sequence as per expected ACK packet
 if (b == ackPacket[ackByteID]) {
 ackByteID++;
 }
 else {
 ackByteID = 0; // Reset and look again, invalid order
 }
 }
 }
}

void setGPS_PowerSaveMode() {
  // Power Save Mode 
  uint8_t setPSM[] = { 
    0xB5, 0x62, 0x06, 0x11, 0x02, 0x00, 0x08, 0x01, 0x22, 0x92           }; // Setup for Power Save Mode (Default Cyclic 1s)
  sendUBX(setPSM, sizeof(setPSM)/sizeof(uint8_t));
}

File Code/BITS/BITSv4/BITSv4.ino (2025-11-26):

 //UMD Nearspace Iridium Tracking Payload (BITS) {Balloon Iridium Tracking System)
//Written by Jonathan Molter and Luke Renegar
//Uses an Iridium 9603 SBD Modem for effective unlimited range, without the need for our own RF blackmagics*
//This software is specifically written with the bits3 board revisision in mind
// ACTIVE REV, 7/25/20

// Runs on Teensy 3.2

#include <XBee.h> //If using 900HP's this must be the custom cpp (or really any post gen2 XBees)
#include <IridiumSBD.h>
#include <SD.h>
#include <TinyGPSPlus.h>

//Serial Ports (sketch requires 4 {Wellll technically 3 + DEBUG})
#define OutputSerial Serial     //USB debug
#define IridiumSerial Serial1   //Iridium 9603
#define XBeeSerial Serial2      //XBee
#define gpsserial Serial3       //GPS

//Pins
#define SLEEP_PIN_NO 5    // Iridium Sleep Pin
#define RING_PIN_NO 2    // Iridium Ring Alert Pin
#define NET_AV_PIN 3
#define chipSelect 6      // Pin for SPI (6 on new board)
#define greenLED 4        // Green Status LED
#define bat_cell1 22

// Config Settings
#define DIAGNOSTICS false // Change this to see diagnostics
#define XBEE_DEBUG true
const bool USEGPS = true; // Should be true 99% of the time
const bool sendingMessages = true; // Whether or not the device is sending messages; begins as true TODO

//Setting default datarates
#define GPS_BAUD 115200
#define SBD_BAUD 19200

//XBee Addresses
const uint32_t BitsSL = 0x417B4A3B;   //BITS (white)Specific to the XBee on Bits (the Serial Low address value)
const uint32_t GroundSL = 0x417B4A36; //GroundStations (u.fl)
const uint32_t BlueSL = 0x417B4A3A;   //Blue (Blue Tape)
const uint32_t WireSL = 0x419091AC;   //Wire (wire antenna)
const uint32_t GHOULSL = 0x4256DDBC;  //GHOUL
const uint32_t UniSH = 0x0013A200;    //Common across any and all XBees

//XBee object / global variables
XBee xbee = XBee();
XBeeResponse response = XBeeResponse();
ZBTxStatusResponse txStatus = ZBTxStatusResponse();
ZBRxResponse rx = ZBRxResponse();
ModemStatusResponse msr = ModemStatusResponse();
const int xbeeRecBufSize = 49; //Rec must be ~15bytes larger than send
const int xbeeSendBufSize = 34;
uint8_t xbeeRecBuf[xbeeRecBufSize];
uint8_t xbeeSendBuf[xbeeSendBufSize];

//GPS data struct and object
struct GPSdata{
  float GPSLat=-1;
  float GPSLon=-1;
  unsigned long GPSTime=-1;
  long GPSAlt=-1;
  int GPSSats=-1;
};
TinyGPSPlus gps;
GPSdata gpsInfo;

//Interval definitions
const long signalCheckInterval = 15000;
unsigned long messageTimeInterval = 60000; // In milliseconds; 300000 is 5 minutes; defines how frequently the program sends messages, now changeable                                                                      

// Hard shutdowns are a bad idea, trace NS-88
//const long shutdownTimeInterval = 14400000; // In milliseconds; 14400000 is 4 hours; defines after what period of time the program stops sending messages
const long gpsLogInterval = 1000;
const long gpsLandedInterval = 1000;

//Initializing Log Files; Must be in form XXXXXXXX.log; no more than 8 'X' characters
File gpsLogFile;
File rxLogFile;
File txLogFile;

const char *gpsLogName =   "GPS.LOG";  //1 sec position/altitude updates
const char *eventLogName = "EVENT.LOG";//Events Iridium/XBee (Special one thanks to Luke)
const char *rxLogName =    "RX.LOG";   //Iridium Uplinks   (toBalloon)
const char *txLogName =    "TX.LOG";   //Iridium Downlinks (toGround)

// Program Timing
unsigned long startTime;
unsigned long lastMillisOfMessage = 0;
unsigned long lastSignalCheck = 0;
unsigned long lastLog = 0;

// Iridium Global Buffers
//#define SBD_RX_BUFFER_SIZE 100 // Max size of an SBD message TODO(1) DELETE
#define maxPacketSize 128		//Standard(GPS/TIME, etc.) + Message Data
#define downlinkMessageSize 100 //Message Data
#define RX_BUF_LENGTH 49		//Uplink Buffer Size

uint8_t rxBuf[RX_BUF_LENGTH]; 			   //Uplink Buffer
//uint8_t sbd_rx_buf[SBD_RX_BUFFER_SIZE];  //TODO(1) DELETE ?(what is this even doing...)
char downlinkMessage2[downlinkMessageSize];//Downlink Buffer
bool downlinkData;

int sbd_csq; //Signal Qual

// The best global
int arm_status = 42;//armed when = 42

// Declare the IridiumSBD object
IridiumSBD modem(IridiumSerial);

//Possible Iridium Error Codes
#define ISBD_SUCCESS             0
#define ISBD_ALREADY_AWAKE       1
#define ISBD_SERIAL_FAILURE      2
#define ISBD_PROTOCOL_ERROR      3
#define ISBD_CANCELLED           4
#define ISBD_NO_MODEM_DETECTED   5
#define ISBD_SBDIX_FATAL_ERROR   6
#define ISBD_SENDRECEIVE_TIMEOUT 7
#define ISBD_RX_OVERFLOW         8
#define ISBD_REENTRANT           9
#define ISBD_IS_ASLEEP           10
#define ISBD_NO_SLEEP_PIN        11
#define SBD

void setup()
{
  Serial.begin(115200);
  Serial2.begin(9600);
  IridiumSerial.begin(SBD_BAUD);
  
  delay(1000);
  Serial.println("BITSrev4");
  
  gps_init(); //Setup the GPS
  
  
  xbee.setSerial(Serial2);
  startBlinks();

//Open Files
  SD.begin(chipSelect);
  gpsLogFile = SD.open(gpsLogName, FILE_WRITE);
  rxLogFile = SD.open(rxLogName, FILE_WRITE);
  txLogFile = SD.open(txLogName, FILE_WRITE);
  delay(10);
  gpsLogFile.println("INIT_GPS_LOG");
  rxLogFile.println("INIT_RX_LOG");
  txLogFile.println("INIT_TX_LOG");
  gpsLogFile.flush();
  rxLogFile.flush();
  txLogFile.flush();
  Serial.println("MadeLogs");
  logprintln("INIT_LOG_LOG");

  //memset(sbd_rx_buf, 0, SBD_RX_BUFFER_SIZE); //TODO(1) DELETE ?

  //XBee Init Message to ground stations
  String("Init").getBytes(xbeeSendBuf,xbeeSendBufSize);   //Convert "Init" 2 bytes, dump into Message buffer
  xbeeSend(GroundSL,xbeeSendBuf);                         //(Target,Message)
  
  int err;
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

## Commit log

2020-01-08 Initial commit with boards
    [bits.brd, bits.sch, cell.brd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]
2020-01-09 Routed cell tracker board with power reg
    [Test_Reg.brd, Test_Reg.sch]
2020-01-18 Cell tracker V3 routed
    [cell.brd, cell.sch]
2020-01-19 Cleaned up the BITS schematic
    [bits.brd, bits.sch]
2020-01-19 cleaned up cell schematic
    [cell.sch]
2020-01-20 Removing 3v3 line, fixing the MOSFET I broke
2020-01-20 Cell Mosfet swap
    [bits.sch]
2020-01-20 General board parts placement for BITS
    [bits.brd, cell.brd]
2020-01-21 Dump of CAD files
    [10x Pinheader Male.prt, 8030T160_WEBBING GUIDE.STEP, 8030T160_WEBBING GUIDE_step.prt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]
2020-01-21 reverted bits schematic back to my last commit"
    [bits.sch]
2020-01-21 Revert "reverted bits schematic back to my last commit""
    This reverts commit d8380e26c9c134d67ee78542be9b2ca2b8e420f0.
    [bits.sch]
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2020-01-21 Maybe fixing supply 1
    [bits.sch]
2020-01-21 v7 Compatible file upload
    [bitsClassic.brd, bitsClassic.sch]
2020-01-21 Integrate the BITS XBee
    [bits.brd, bits.sch]
2020-01-21 Updated the inductor and mosfet in cell schematic
    [91225A111_PHENOLIC FLAT WASHER_step.prt, cell.brd, cell.sch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]
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2020-01-22 Created an alternate board
    [bitsClassicEdit.brd, bitsClassicEdit.sch]
2020-01-22 bits board try 2
    [bitsClassicEdit.brd, bitsClassicEdit.sch]
2020-01-23 put connector on cell board, plus lots of cad work
    [132123_3d_model_file.stp, 132123_3d_model_file_stp.prt, 732511150.stp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]
2020-01-24 a whole lot of finshed nonsense
    [1053071202.stp, 1053071202_stp.prt, 1053111202.stp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]
2020-02-04 All of the changes with CAD and electronics since switching to the microclasp connectors
    [132119_3d_model.stp, 132119_3d_model_stp.prt, 513820200.stp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]
2020-02-05 fixes and design review slides
    [513820400.stp, 513820400_stp.prt, 559320430.stp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]
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2020-05-13 Reorganizing files for new boards
    [cell.brd, cell.sch]
2020-05-13 Fixing Errors, ditching coincell
    [cell.brd, cell.sch]
2020-05-16 Fixing BITS brd
    [bits.brd, bits.sch, bits3.2.brd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]
2020-05-19 Bunches of CAD, but I don't like CAD
    [AseemSecondBox.prt, AseemSecondBoxv2.prt, Command_Module.prt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]
2020-05-29 Box Passthroughs, fixing Iridium Board
    [LVC.prt, RockBLOCK V 3B3479.prt, RockBLOCK_9603_stp.prt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]
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2020-06-19 updating resistors for correct cutoff
    [cell.brd]
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2020-07-03 Moved libs, adding isolator
    [cell.brd]
2020-07-04 More stuff, close, not done
    [bits3.2.brd, bits3.2.sch]
2020-07-05 Finishing touches for Cell3.2
    [bits3.2.brd, cell_3.2.brd, cell_3.2.sch]
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2020-07-12 Final board export/cam, code libraries fld
    [bits3.2.brd, cell_3.2.brd]
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2020-07-14 minor R val changes, STEP generation
    [0.2F.prt, 1.575GHz.prt, 10 uF.prt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]
2020-07-26 API testing/cellv3.1trigger software failREP
    [BITSrev3v1.ino, XBeeMethods.ino, bitsGPSmethods.ino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]
2020-07-26 Added board step files to CAD fld
    [bits3.2.step, bitsv3_2.step, cell_3.2.step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]
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2021-01-09 Trying some new hardware configs
    [AseemSecondBox.prt, cell_box.prt, cell_box_half.prt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]
2021-01-11 changing some colors and taking screenshots
    [10x Pinheader Male.prt, 132123_3d_model_file_stp.prt, 513820400_stp.prt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]
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2021-01-20 plate mounting bolt holes
    [teriarybox_plate.prt, tertiarybox.prt, tertiaryboxAsem.prt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]
2021-01-25 Adding a copy of the AdafruitRFM95 board for ref
    [Adafruit Feather M0 RFMxx.brd, Adafruit Feather M0 RFMxx.sch]
2021-01-25 LightAPRS switching reg/LVC updates
    [Adafruit Feather M0 RFMxx.brd, Adafruit Feather M0 RFMxx.sch, lvc.brd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]
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2021-02-01 Cutting down the adafruit rfm board
    [Adafruit Feather M0 RFMxx.sch, SimplePayload.sch, lvc_v2.brd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]
2021-02-20 box fixes
    [SimplePayload.sch, teriarybox_plate.prt, tertiarybox.prt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]
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2021-03-18 Adding in Bitsv2 board CAD
    [bits2.brd, bits2.sch]
2021-03-18 re-order/confirm LVC fix
    [lvc_v2.brd]
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2021-04-03 new_reg work
    LMR50410XF reg design to cover and possibly replace LMR16020 for <1A command things
    [new_reg.sch]
2021-07-06 plate for v2 bits brd
    [teriarybox_plate_bitsv2.prt]
2021-08-08 re-arrange some file structure, init boxv4
    [AseemSecondBox.prt, Command_Module.prt, boxAssemv4.prt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]
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2021-08-19 New reg board
    LM20242
    [test_reg.brd, test_reg.sch]
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2021-09-26 improved spacing between rockblock and bits board on plate
    [boxPlatev4.prt]
2021-10-03 BITSv4
    omg I need a clock so bad
    [BITSv4.brd, BITSv4.sch]
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2023-07-31 bits v5 board begins
    [BITSv5.kicad_pcb, BITSv5.kicad_sch, BOM.xlsx]
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2023-08-11 BITSv5 sch almost done
    [BITSv5.kicad_pcb, BITSv5.kicad_sch, BOM.xlsx]
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2023-08-18 bits v5 board nearly done
    [BITSv5.kicad_pcb, BITSv5.kicad_sch, BOM.xlsx]
2023-08-19 several hundred bits v5 errors later
    [BITSv5.kicad_pcb, BITSv5.kicad_sch]
2023-08-20 bits v5 board feedback added
    [BITSv5.kicad_pcb, BITSv5.kicad_sch, BOM.xlsx]
2023-08-20 no more 5 am commits
    [BITSv5.kicad_pcb]
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2023-08-25 small update to BITSv5 for review
    [BITSv5.kicad_pcb, BITSv5.kicad_sch, BOM.xlsx]
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2023-08-26 xbee joint board begins
    [XBee_Joint.kicad_pcb, XBee_Joint.kicad_sch]
2023-08-28 xbee joint board updates
    [XBee_Joint.kicad_pcb, XBee_Joint.kicad_sch]
2023-08-30 xbee joint and bits updates
    [BITSv5.kicad_pcb, BITSv5.kicad_sch, BOM.xlsx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]
2023-09-04 most up to date bits and xbee joint
    [XBee_Joint.kicad_pcb]
2023-09-04 added button to BITS5
    [BITSv4.kicad_pcb, BITSv4.kicad_sch, BITSv5.kicad_pcb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]
2023-09-04 working on xbee joint
    [XBee_Joint.kicad_pcb, XBee_Joint.kicad_sch]
2023-09-05 xbee joint layout almost complete
    [XBee_Joint.kicad_pcb, XBee_Joint.kicad_sch]
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2023-09-05 BITSv5 added additional Xbee connector
    [BITSv5.kicad_pcb, BITSv5.kicad_sch]
2023-10-19 bits v5 w/ dorji radio
    [BITSv5-B_Cu.gbr, BITSv5-B_Mask.gbr, BITSv5-B_Paste.gbr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]
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2023-10-23 ordered new joint and bits
    [BITSv5.kicad_sch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]
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2023-11-11 transmit and receive on BITS and (Not)Xbee Joint, packets are recognized (valid preamble detected) but a header error is thrown on receive (LoRa header CRC error)
    [SX1262.cpp, SX1262.h, test.cpp]
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2023-11-29 more (not)xbee joint futzing, still doesn't work :(
    [SX1262.cpp, SX1262.h, test.cpp]
2023-12-10 init SX1262 lib and hopefully fix crusty submodule issue
    [(Not)XBee_Joint.h, SX1262.cpp, SX1262.h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]
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2024-01-31 changed BITSv5 antennas to ufl, added TIMEPULSE and EXTINT GPIOs, and exposed GPIO UART over header
    [BITSv5.kicad_pcb, BITSv5.kicad_sch]
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2024-02-01 nvm I want BITSv5 to have a chip antenna
    [BITSv5.kicad_pcb, BITSv5.kicad_sch]
2024-02-01 finished GPS chip antenna, removed SOICbite for test points because couldn't find space
    [BITSv5.kicad_pcb, BITSv5.kicad_sch]
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2024-02-14 tried to see if new txen fix for the radio would make the GPS magically work but it didn't :(
    [test.cpp]
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2024-03-02 fixed FRAM library include for (Not)Xbee Joint
    [test.cpp]
2024-03-03 fixed Models:Drawings
    [BITSv5-1.step, out.stl]
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2024-03-26 iridium driver updates, SBDIX parsing broken but basics confirmed working
    [BITSv5.h, iridium-lib.cpp, iridium-lib.h]
2025-02-27 tested basic functionality, def some issues to work out, also added channel activity detection which needs to be tested
    [radio_test.cpp]
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

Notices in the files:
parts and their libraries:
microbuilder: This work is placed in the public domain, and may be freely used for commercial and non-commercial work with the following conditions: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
